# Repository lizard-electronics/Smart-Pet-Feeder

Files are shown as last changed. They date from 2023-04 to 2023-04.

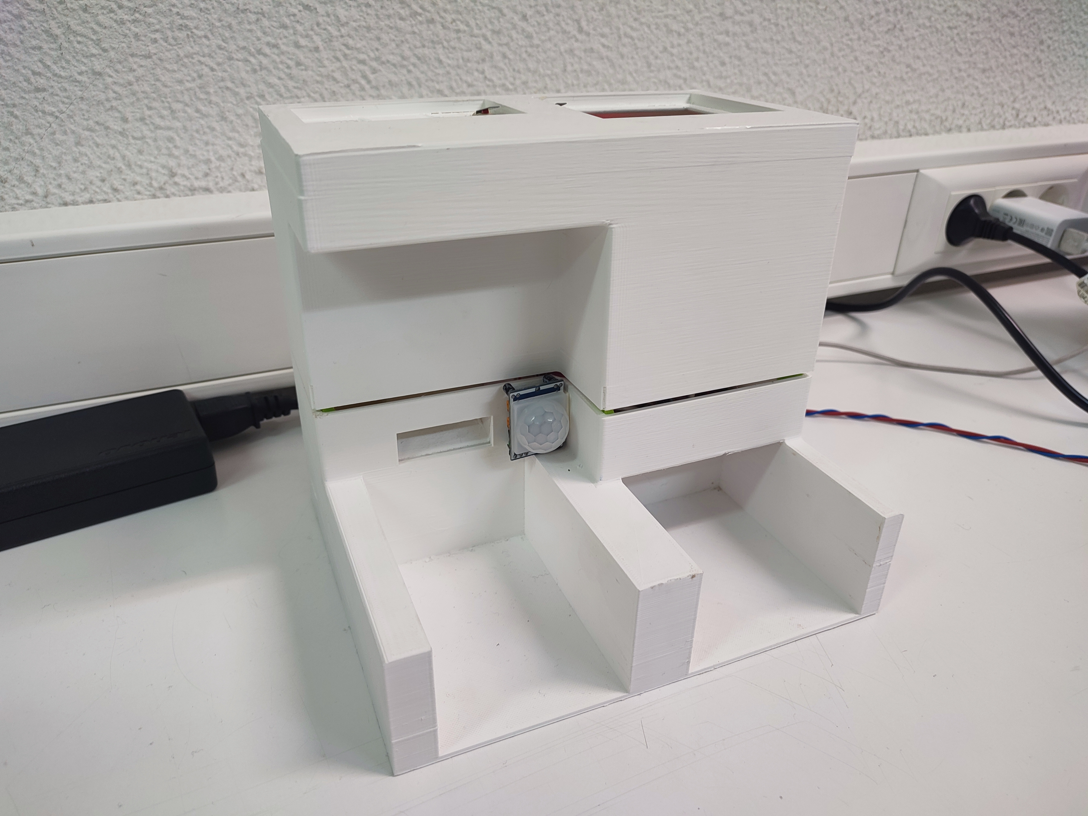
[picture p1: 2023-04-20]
Pictures/SmartPetFeeder_FinalResult.jpg

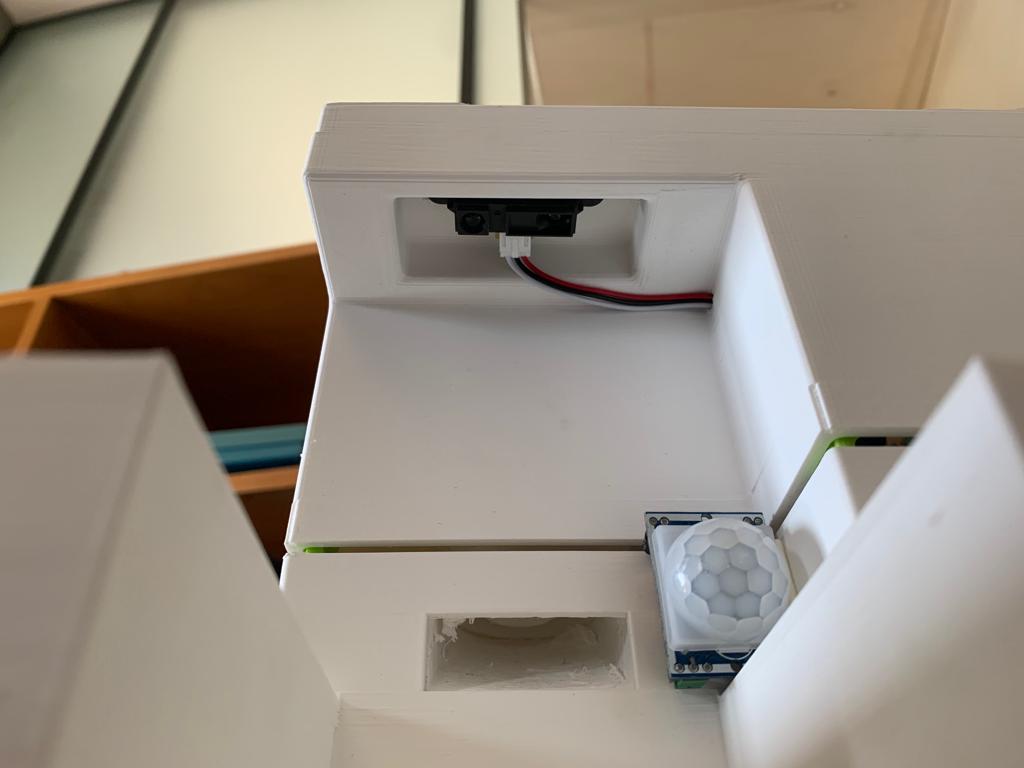
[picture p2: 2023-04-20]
Pictures/SmartPetFeeder_FoodSensor.jpg

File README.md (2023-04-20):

# Smart-Pet-Feeder

College project developed for the Internet of Things course.

Developed the firmware for an ESP32 using FreeRTOS to control the hardware and communicate through MQTT the Pet Feeder’s food and water status to a Data Base implemented on a Raspberry Pi (Node-RED).

*IPS - Escola Superior de Tecnologia de Setúbal*  
*Licenciatura em Engenharia Eletrotécnica e de Computadores*  
*Projeto de Internet das Coisas*  
2022/2023

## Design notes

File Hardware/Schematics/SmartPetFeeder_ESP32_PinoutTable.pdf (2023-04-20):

Name | Type | J2 | Left | Battery Up | Right | J1 | Name | Type
| | | NC | | NC
| POWER | 1 | 5V | | CLK
| | | CMD | | SD0
| | | SD3 | | SD1
| | | SD2 | | 15 | 1 | VALVE_WATER | GPIO_OUTPUT
SENSOR_PIR | GPIO_INPUT | 2 | 13 | 2 | RESERVED2 | GPIO
| POWER | | GND | | 0 | 2 | LED_NOTIFICATION | GPIO_OUTPUT
12 | 4 | 3 | LED_LEVEL | GPIO_OUTPUT
TRIG_DISPENSER | GPIO_OUTPUT | 4 | 14 | 16 | 4 | LED_STATE | GPIO_OUTPUT
ECHO_DISPENSER | GPIO_INPUT | 5 | 27 | | 17 | 5 | STEPPER_IN4 | GPIO_OUTPUT
| | 6 | 26 | | 5 | 6 | STEPPER_IN3 | GPIO_OUTPUT
| | 7 | 25 | | 18 | 7 | STEPPER_IN2 | GPIO_OUTPUT
SENSOR_WATER | GPIO_INPUT | 8 | 33 | | 19 | 8 | STEPPER_IN1 | GPIO_OUTPUT
SWITCH_LID | GPIO_INPUT | 9 | 32 | GND | POWER
SWITCH_BOWL | GPIO_INPUT | 10 | 35 | 21 | RESERVED21 | GPIO
BUTTON_MAINTENANCE | GPIO_INPUT | 11 | 34 | | RX
SENSOR_FOOD | GPIO_INPUT | 3 | SVN | | TX
SVP | 22 | RESERVED22 | GPIO
BUTTON_RESET | GPIO_INPUT | 12 | EN | 23 | RESERVED23 | GPIO
| POWER | 13 | 3V3 | | GND | 10,11,12 | | POWER

Buttons/Switches
Ultrassonic Level Sensors
PIR Sensor
Solenoid Valve
LEDs
Stepper Motor
5V
3V3
GND

ESP32

Color Legend

#define SENSOR_PIR_GPIO_INPUT 13 | #define VALVE_WATER_GPIO_OUTPUT 15

| #define RESERVED2_GPIO 2
#define TRIG_DISPENSER_ 12 | #define LED_NOTIFICATION_GPIO_OUTPUT 0

#define ECHO_DISPENSER_GPIO_OUTPUT 14 | #define LED_LEVEL_GPIO_OUTPUT 4

#define TRIG_FOOD_GPIO_INPUT 27 | #define LED_STATE_GPIO_OUTPUT 16

#define ECHO_FOOD_ 26 | #define STEPPER_IN4_GPIO_OUTPUT 17

#define TRIG_WATER_ 25 | #define STEPPER_IN3_GPIO_OUTPUT 5

#define ECHO_WATER_GPIO_INPUT 33 | #define STEPPER_IN2_GPIO_OUTPUT 18

#define SWITCH_LID_GPIO_INPUT 32 | #define STEPPER_IN1_GPIO_OUTPUT 19

#define SWITCH_BOWL_GPIO_INPUT 35

#define BUTTON_MAINTENANCE_GPIO_INPUT 34 | #define RESERVED21_GPIO 21

#define RESERVED22_GPIO 22 #define RESERVED23_GPIO 23

TRIG_FOOD
ECHO_FOOD
TRIG_WATER
ECHO_WATER

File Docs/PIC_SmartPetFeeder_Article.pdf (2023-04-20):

# Smart Pet Feeder

Escola Superior de Tecnologia de Setúbal Licenciatura em Engenharia Eletrotécnica e de Computadores, Projeto em Internet das Coisas

Eduardo Silva [Database] | 202001449@estudantes.ips.pt
Guilherme Correia [Mobile App] | 202002058@estudantes.ips.pt
João Reis [Node-RED & 3D Model] | 200500970@estudantes.ips.pt
Manuel Lagarto [Firmware] | 202002147@estudantes.ips.pt
Rui Colaço [Hardware] | 199100317@estudantes.ips.pt
I. INTRODUCTION

Most of the time, pet owners spend their time away from home and away from their pet friends, whether during vacation or work, leaving them a certain quantity of food and water which may get spoiled or be spilled away accidentally by the animal.

To solve these problems was created the Smart Pet Feeder, which provides pet owners with an innovative way to keep their furry friends well-fed, from monitoring their feeding habits to scheduling portion sizes based on veterinary advice.

This solution consists of the main device, the Pet Feeder that pairs with the Central Hub through a wireless connection. With this method, pairing more than one Pet Feeder to a single Central Hub is possible.

The Pet Feeder can feed both food and water, where the food is stored in an internal dispenser with an integrated stepper motor for precision portion control, and the water is regulated through a valve connected to the house’s water line. A set of sensors implemented in the Pet Feeder constantly monitors and transmits to the Central Hub the food and water levels in the bowls and dispenser, as well as the animal presence.

The Central Hub is implemented with a 7-inch display that displays each Pet Feeder’s dashboard. These dashboards show the levels of each Pet Feeder, as well as the important notifications and scheduled portions. All the data needed by the Central Hub and the rest of the systems are stored in the integrated database.

A mobile app for Android users is also available for the Smart Pet Feeder. With this app, pet owners can schedule portions based on veterinary advice, monitor feeding habits, control the connected devices, receive push notifications, and many more features that make the Smart Pet Feeder more interactive.

To summarize, the Smart Pet Feeder has different features that increase the quality of life of pets and allow pet owners more ease in feeding and monitoring the animal, for example:

- Scheduled portions of food and water.
- Pet Feeder’s state monitoring.
- Feeding habits monitoring.
- Mobile app notifications and warnings.
- Minimalist and compact design.
- Be integrated into the pet owner’s house or in an institution.

II. STATE OF THE ART

The industry of Smart Pet Feeders is increasing daily with many models appearing on the market with scheduling and monitoring capabilities, being one of the biggest takes of the Internet of Things revolution.

While most Smart Pet Feeders can only control the dispensed food based only a schedule defined by the pet owner, there are pet feeders that can also monitor the feeding habits, do self-tests, and integrate their data with the main Smart Home app. An example is the XIAOMI® Smart Pet Feeder.

On the other hand, one feature that all the Smart Pet Feeders available on the market share is providing pet owners the convenience and ease of feeding their furry friends, ensuring their pets are well-fed and hydrated even when their owners are away from home during vacation or work.

III. SYSTEM DESCRIPTION

The Smart Pet Feeder is based on two main components, the ESP32, and the Raspberry Pi microcontrollers, used in the Pet Feeder and Central Hub devices (Figure 1), respectively.

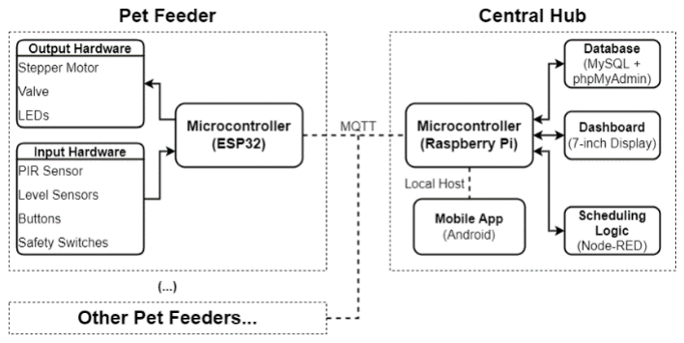
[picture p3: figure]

Figure 1 - Smart Pet Feeder Block Diagram.
The Pet Feeder is where the hardware to interface with the pet feeding process is implemented and has the following components: an ESP32, a Stepper Motor, a Valve, a PIR Sensor, two IR Level Sensors, an Ultrasonic Level Sensor, three LEDs, two Push Buttons and three Safety Switches.

The Central Hub is used to pair the installed Pet Feeders via the MQTT communication protocol and is where the scheduling control logic, Pet Feeder dashboard, and interface with the database are implemented. This device is composed of the Raspberry Pi and a 7-inch display.

Hardware
The Pet Feeder hardware schematic (Figure 2) was designed using KiCad, an open-source EDA software for hardware and PCB design.

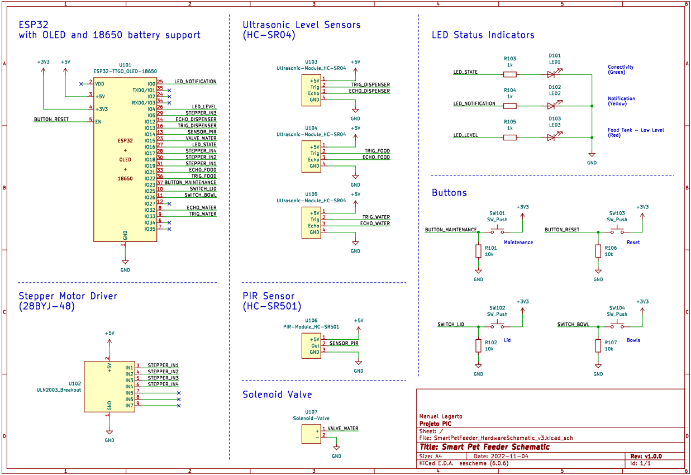
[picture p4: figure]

Figure 2 - Pet Feeder electrical hardware schematic.
The main control board integrates the ESP32 Board socket and all the screw-type terminal connectors for the sensors and actuators signals, allowing seamless maintenance and integration.

To rotate the paddle wheel to therefore control the amount of food purged through the nozzle, the 28BYJ-48 Stepper Motor, which pairs with the ULN2003 Driver, was selected. This Stepper Motor has four coil windings and delivers 64 steps per turn, corresponding to 5,625 degrees of precision. As the motor consumes about 217mA of current, the ESP32 board can’t supply the driver so an external power supply of 5V DC is required.

To regulate the water feeding was selected a generic one-way Solenoid Water Valve. An external power supply of 12V DC is required to command this valve.

As it is necessary three types of external power supply – main control board (5V), Stepper Motor (5V), and Solenoid Valve (12V) – a three-stage power supply was designed (Figure 3). The selected ESP32 board already has a 3.3V regulator.

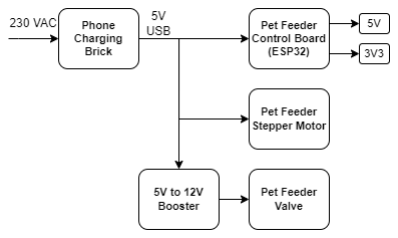
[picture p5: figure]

Figure 3 - Three-stage power supply.
For animal presence detection, the HC-SR501 PIR Sensor was selected, which uses an infrared LED. This sensor is placed at the front of the device and has 110 degrees of detection angle, supplied with 5V DC from the main control board.

Inside the Pet Feeder are placed three level
sensors. | Two | of them | are | the | SHARP
GP2Y0A21YK0F, mounted above the food and water bowls to measure its levels with infrared technology. These sensors offer better precision for harsh environments but are more expensive, so an HC-SR04 Ultrasonic Sensor was mounted inside the dispenser to measure its level, which is a closed and more controlled environment.

A set of LEDs and Buttons is mounted on the side of the Pet Feeder to give a user interface to the pet owner. A green LED indicates the state of the connectivity, a yellow LED indicates an unread notification, and a red LED indicates the low level of food in the dispenser. One of the buttons does a manual purge of the food and the other resets the system.

Three Safety Switches are mounted to stop the system in case one of the lids or the bowls are removed from the Pet Feeder.

Firmware
The firmware for the Pet Feeder is based on the dual-core ESP32 microcontroller and developed using the C++ programming language and the FreeRTOS operating system [www.freertos.org], natively supported by the Arduino framework.

All the firmware was developed with the Visual Studio Code code editor, with the extension PlatformIO to give it IDE capabilities to upload and debug the program in the ESP32.

The FreeRTOS is a real-time operating system used in embedded systems that require multi-tasking operation, and this project is no exception.

For this firmware, a set of tasks were created where the tasks related to the input/output hardware are pinned to the ESP32 Core0 (Figure 4 & Figure 5), and the tasks related to the MQTT communication are pinned to the ESP32 Core1 (Figure 6). With this method, it's possible to guarantee that the MQTT connectivity with the Central Hub is never interrupted.

Figure 4 - Input hardware FreeRTOS tasks.

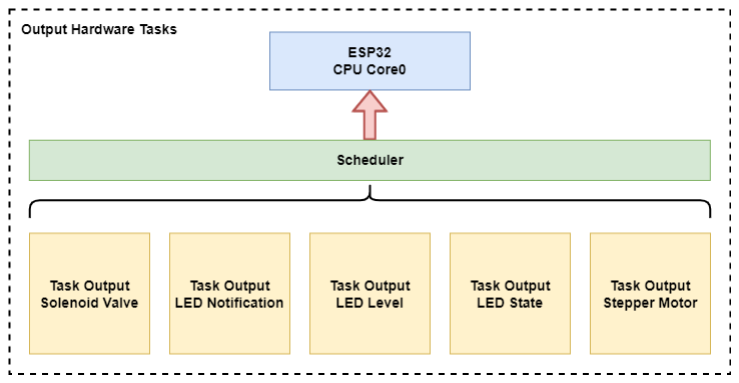
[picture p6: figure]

Figure 5 - Output hardware FreeRTOS tasks.

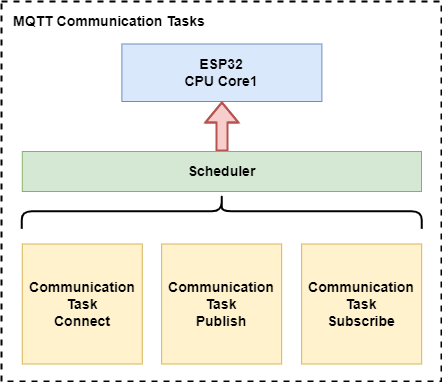
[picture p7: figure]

Figure 6 - MQTT communication FreeRTOS tasks.
To pass data between different tasks, a Queue Management API is available in FreeRTOS. With this method, it’s possible to safely pass information between the MQTT communication tasks and the I/O hardware tasks, by implementing the subscribe_queue and the publish_queue (Figure 7). The xQueueSend() function sends data to the queue, and the xQueueReceive() function waits for data to arrive in the queue.

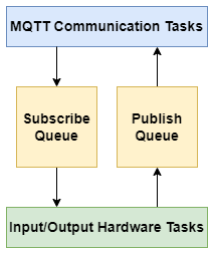
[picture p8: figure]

Figure 7 - Intertask communication diagram.
The MQTT protocol is largely used in IoT devices by using the server’s IP address, in this case, the Raspberry Pi installed on the Central Hub, to communicate over a wireless network connection. Each packet of communication data is composed of a topic and a message, i.e., the sensor id and the sensor data, respectively.

As seen in Figure 8, the Firmware flowchart is illustrated, representing the control algorithms and the interactions between each task. The complete code developed for the Firmware is attached at the end of this article.

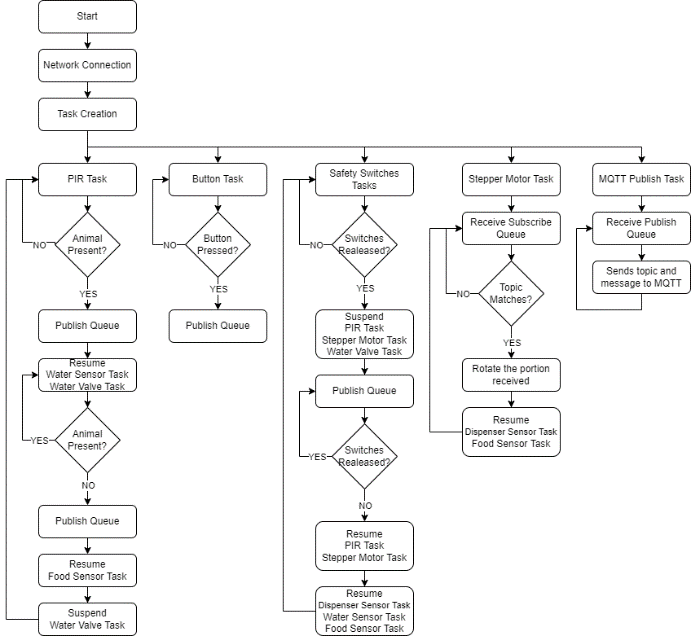
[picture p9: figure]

Figure 8 - Firmware's flowchart.
The interaction between each hardware task is done by the Task Control API available in FreeRTOS, which includes vTaskSuspend() and vTaskResume() functions. A task resumes its operation from the instant it was previously suspended.

Database
The Database for the Smart Pet Feeder stores all the data needed for the schedules of portions, pet owner login, feeding habits, pet information, and other important data for the system operation.

The relational model (Figure 9) was developed
with | the | ERDPlus | online | modeling | tool
(https://erdplus.com/). This model represents the tables (entities) used in the database to store the data, the data types of each attribute, and the relationships between each entity.

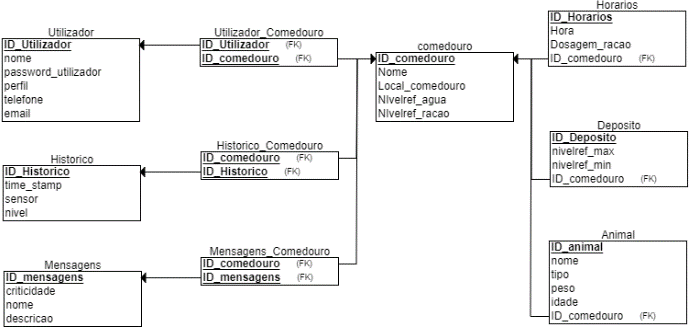
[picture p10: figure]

Figure 9 - Relation model planned for the Database.
Next, the Database was created with the MySQL Workbench software according to the previous model, using the DDL and DML languages.

To host and manage the created Database it was used the web application phpMyAdmin configured in the Raspberry Pi of the Central Hub, which makes use of .php scripts to a system interact with the Database. This application provides a web interface to manage and debug the Database which greatly eases the operation, creation, and maintenance of the Database.

Mobile App
With the Mobile App pet owners can have a personal user login to access the paired devices to the Central Hub, see the Pet Feeder status, schedule portions of meals based on the veterinary advice or animal’s metabolism, receive important notifications, and update the user information.

The app was developed with the Android Studio IDE using Java, JavaScript, HTML, and CSS programming languages. For the app was developed a flowchart (Figure 10) for the navigation between the different menus. After launching the app, the user will be prompted with the login screen that leads to the main page corresponding to the devices list. From this page, the user can access the side menu screen to access the other menus, such as schedule, feeder status, notifications, and devices list.

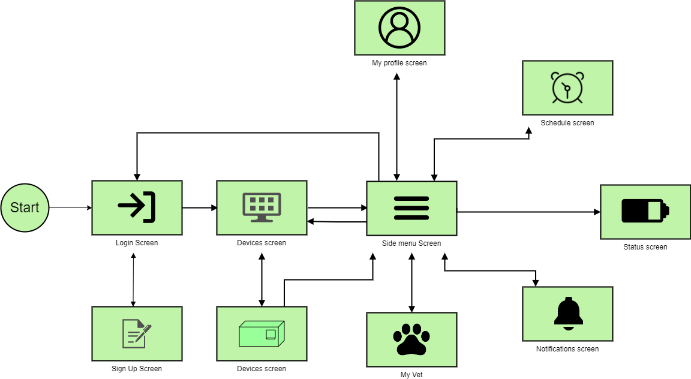
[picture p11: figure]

Figure 10 - Mobile App menu navigation flowchart.
To use this app, it’s necessary to always be connected to the same Smart Pet Feeder network because the app is constantly communicating with the database through the PHP functions, to realize queries and updates in the Database.

Figure 11 represents the user registration and login page menu in the app where the pet owner must insert his personal information.

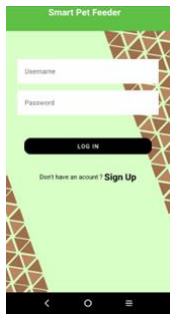
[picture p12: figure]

Figure 11 - Mobile App user registration and login page.
Figure 12 represents the Mobile App side panel where the user can navigate through all the menus available in the app.

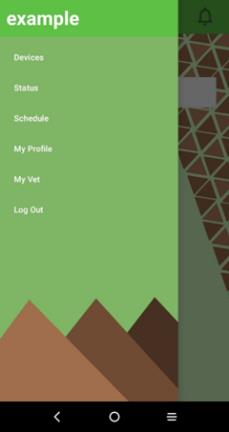
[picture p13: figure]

Figure 12 - Mobile App side panel.
Figure 13 represents the pairing process of a Pet Feeder to the Central Hub, by scanning its QR Code, and the menu of the paired device list.

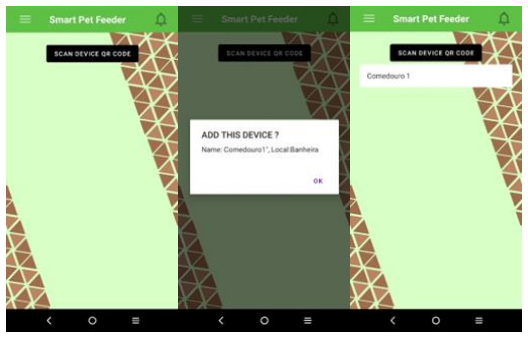
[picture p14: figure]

Figure 13 - Mobile App pairing process of a Pet Feeder.
Figure 14 represents the Pet Feeder’s status page where is shown the assigned name, bowls, and dispenser levels and its home location.

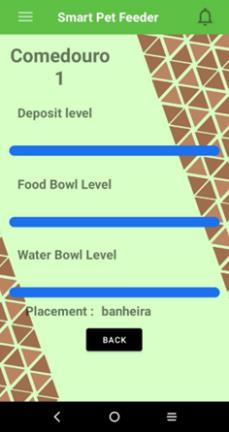
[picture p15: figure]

Figure 14 - Mobile App Pet Feeder's status page.
Figure 15 represents the animal’s scheduled meals where a new one can be added by inserting its time and portions.

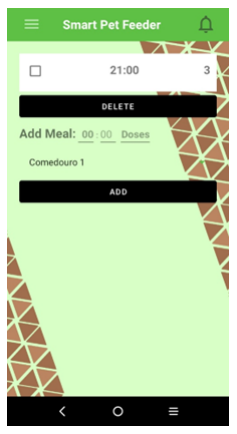
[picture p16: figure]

Figure 15 - Mobile App scheduled meals page.
Figure 16 represents the page to associate each animal to each Pet Feeder, by inserting their information and the pretended Pet Feeder id. On this page is also possible to view a list of the already associated animals to the app.

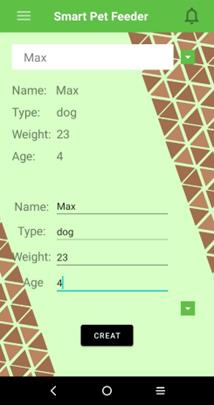
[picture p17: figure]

Figure 16 - Mobile App animal association page.
[Show the menu flow diagram. Explain each app menu]

Software (Node-RED)
Node-RED was used to program the control logic for the scheduling portions and other features of the Smart Pet Feeder. This tool is a web-based programming tool to connect different hardware devices to different APIs and online services.

For the control logic was developed a flowchart (Figure 17 & Figure 18) in which is represented the subscribe and publish functions from the MQTT, and the query/update process on the Database.

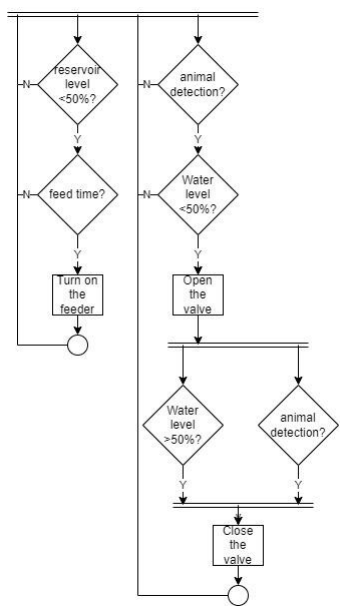
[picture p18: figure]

Figure 17 - Node-RED control logic flowchart, part I.

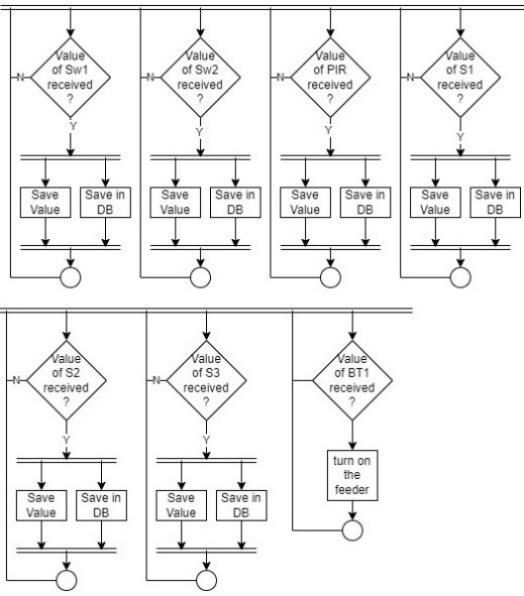
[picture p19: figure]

Figure 18 - Node-RED control logic flowchart, part II.
The control logic (called flows in the Node-RED) was programmed using various types of nodes available from the palette in the development environment of the programming tool. For this project, the two most important types of nodes were the “in/out mqtt” node and the “mysql” node, used to communicate with the Pet Feeder and the Database, respectively.

3D Model
The 3D Model of the Pet Feeder was designed with the Autodesk® Inventor CAD software and manufactured using a 3D printer with PLA filament.

In Figure 19 is represented the 3D front view of the Pet Feeder where the food bowl is located on the left and the water bowl is located on the right.

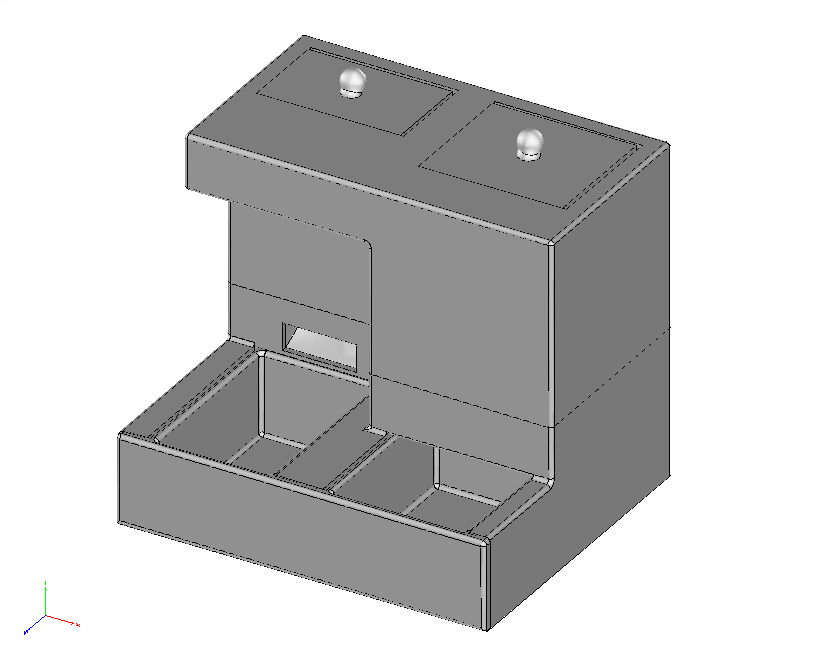
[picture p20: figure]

Figure 19 - Front view of the Pet Feeder’s 3D model.
In Figure 20 the same view is represented but with transparent faces to show the location of the dispenser and the feeding mechanism inside the Pet Feeder.

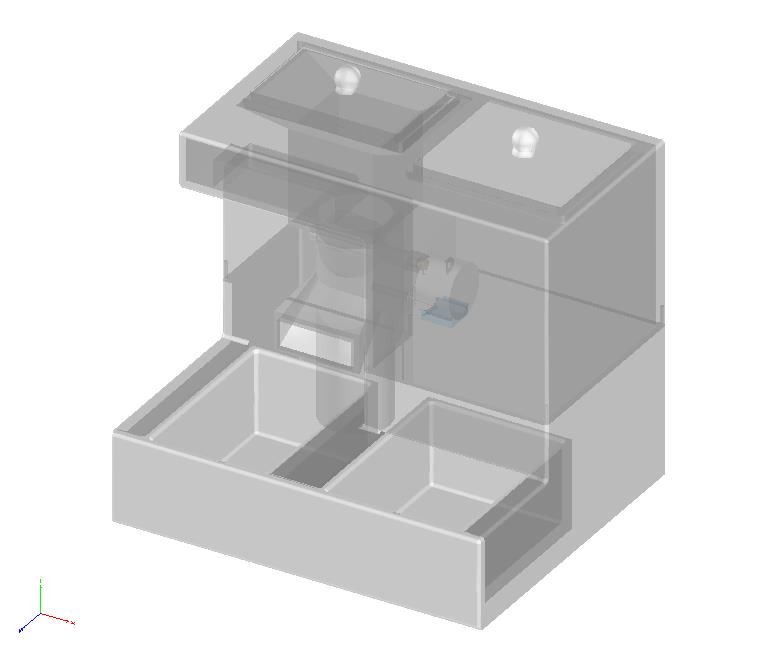
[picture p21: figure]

Figure 20 – Transparent view of the Pet Feeder’s 3D model.
In Figure 21 is represented a cut section of the side view of the Pet Feeder to represent the feeding mechanism under the dispenser.

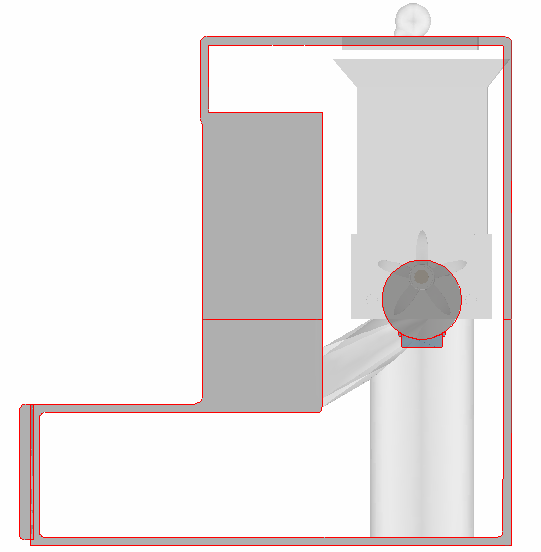
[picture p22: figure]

Figure 21 - Section cut of the Pet Feeder's 3D Model.
This mechanism is directly driven by the Stepper Motor and consists of a paddle wheel with five equally spaced blades that represent each portion of the animal’s food.

After collecting the food from the dispenser with the paddle wheel, the food is directed to a channel that leads to the front of the Pet Feeder, falling into the food bowl right under the exit.

Both the food and the water bowls are removable and integrated into the same part which eases the cleaning process.

IV. FINAL RESULTS

After 3D printing all the parts needed for the Smart Pet Feeder, the Pet Feeder’s model was assembled (Figure 22) with all the electrical hardware wired together and mounted inside (Figure 23).

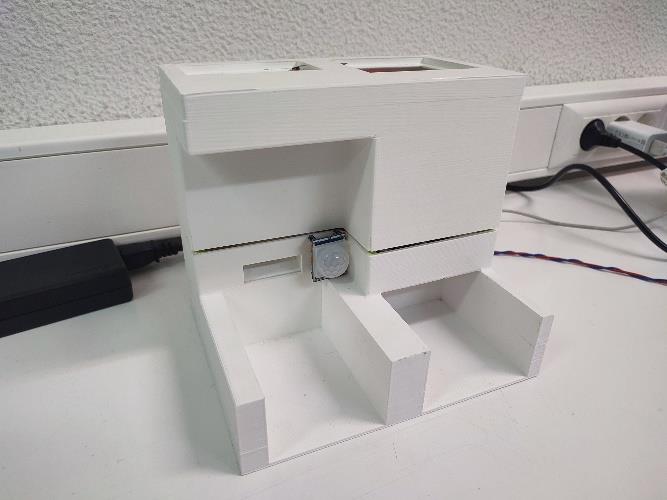
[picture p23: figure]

Figure 22 - Pet Feeder assembled.

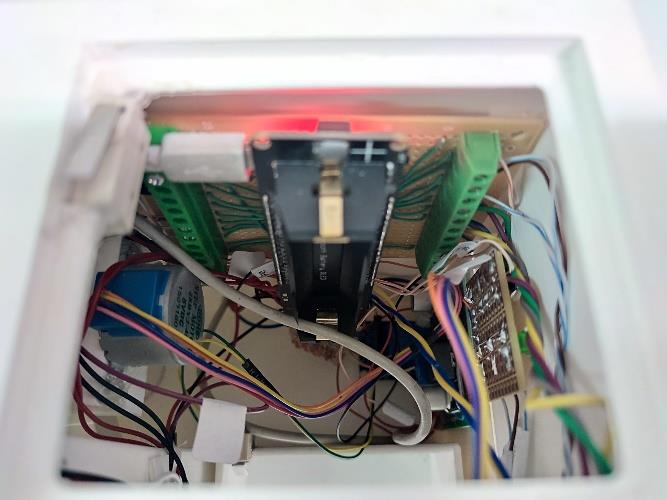
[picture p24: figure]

Figure 23 - Electrical hardware wired inside the Pet Feeder.
Figure 24 shows the LEDs and Buttons assembled on the side of the Pet Feeder, indicating the connected state (Green LED), low food level (Red LED), unread notifications (Yellow LED), manual feed (top button), and reset (bottom button).

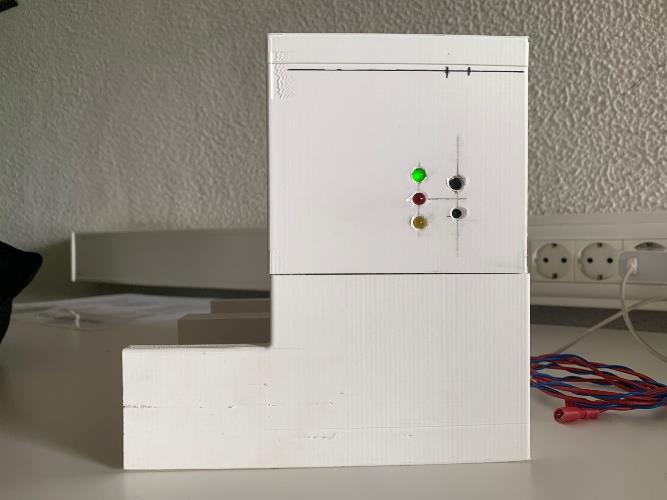
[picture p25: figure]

Figure 24 - LEDs and Buttons mounted on the side.

V. CONCLUSIONS & FUTURE UPDATES

With the development of this project, it was possible to acquire all the skills needed to develop an IoT product from the ground up.

This project addressed different topics that would not be possible to approach in this course. Hardware design where a schematic was designed with all the selected hardware for the project needs. Firmware development where the group was introduced to the FreeRTOS real-time operating system for the first time, which is used for an embedded system with multi-tasking operation. Database design by modeling an entire database according to the data needed for the project. Android app development where the group used Android Studio with different programming languages to develop the Mobile App for the pet owner to interact with the Smart Pet Feeder. Introduction of the Node-RED programming tool which was useful to integrate the different hardware devices with different APIs (Database for example). 3D Model development to 3D print the Pet Feeder concept model.

For the next iteration of the project, the Hardware needs to be integrated into a PCB board to achieve a more compact and eliminate noise in the wiring connections. The stepper motor also needs to be upgraded to a more powerful one, since it was detected a lack of force in the rotation of the paddle wheel during the tests.

VI. REFERENCES

1. KiCad EDA [Link] (https://www.kicad.org/)
2. Visual Studio Code [Link] (https://code.visualstudio.com/)
3. FreeRTOS documentation: [Link] (https://www.freertos.org/a00106.html)
4. ERDPlus database modeling tool [Link] (https://erdplus.com/)
5. Andriod Studio IDE [Link] (https://developer.android.com/studio)
6. Node-RED programming tool [Link] (https://nodered.org/)
7. 28BYJ-48 Stepper Motor datasheet [Link] (https://www.mouser.com/datasheet/2/758/stepd-01-data-sheet-1143075.pdf)
8. ULN2003 Driver datasheet [Link] (https://www.st.com/resource/en/datasheet/uln2001.pdf)
9. SHARP GP2Y0A21YK0F datasheet [Link] (https://global.sharp/products/device/lineup/data/pdf/datasheet/gp2y0a21yk_e.pdf)
10. HC-SR04 Ultrasonic Sensor datasheet [Link] (https://cdn.sparkfun.com/datasheets/Sensors/Proximity/HCSR04.pdf)
11. HC-SR501 PIR Sensor datasheet [Link] (https://www.epitran.it/ebayDrive/datasheet/44.pdf)

VII. ATTACHMENTS

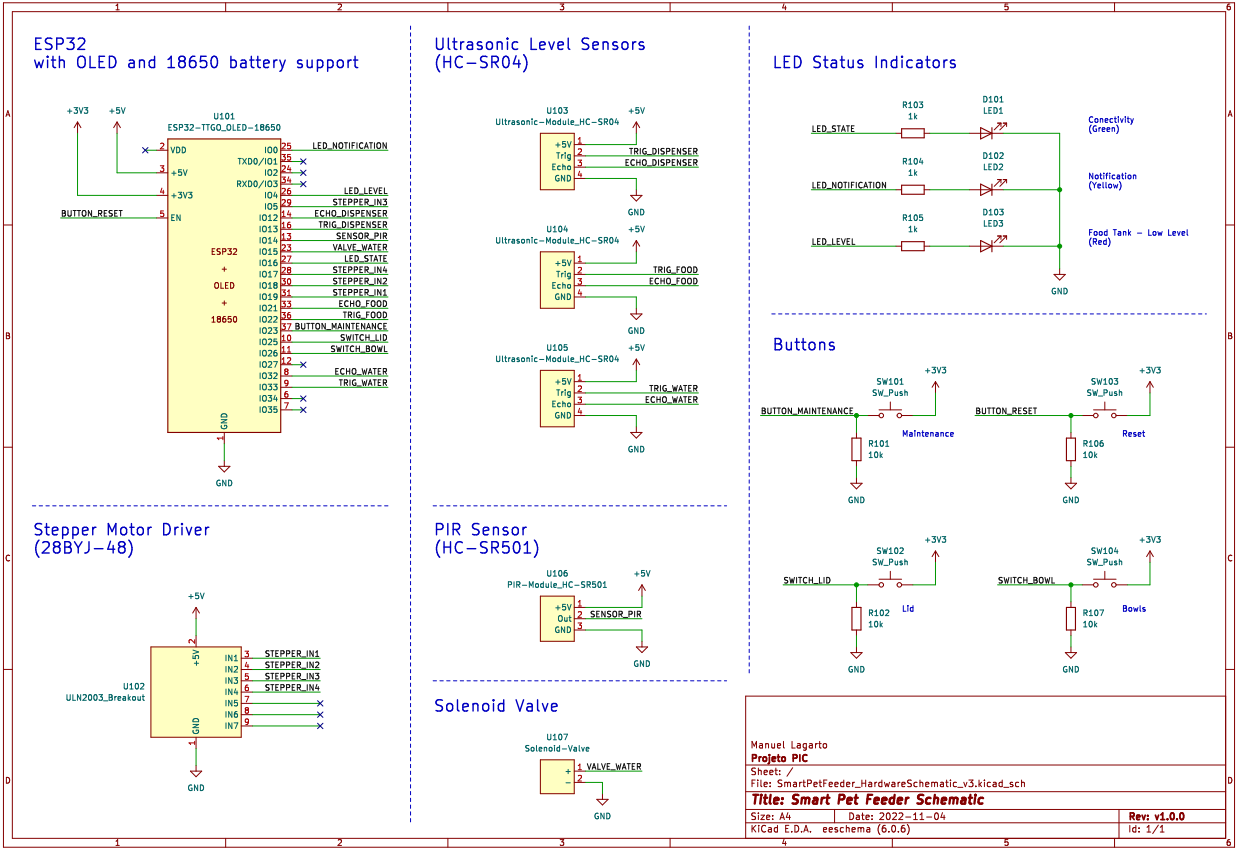
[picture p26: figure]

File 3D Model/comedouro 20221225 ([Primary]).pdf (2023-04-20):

setPageBoxes("Crop", 0, 0, [0,2000,2000,0]);

TITLE PART NO | comedouro 20221225 REVISION DESIGNER | LENOVO ENGINEER NOTES

THE INFORMATION AND/OR MATERIAL IN THIS DOCUMENT IS THE PROPERTY OF AND RESTRICTED INFORMATION AND/OR MATERIAL OF THE AUTHOR. THIS INFORMATION MAY NOT BE USED, REPRODUCED, PUBLISHED OR DISCLOSED TO OTHERS WITHOUT WRITTEN AUTHORIZATION. IT IS TO BE USED ONLY FOR MANUFACTURING ITEMS SPECIFIED WITHIN THE DOCUMENT.

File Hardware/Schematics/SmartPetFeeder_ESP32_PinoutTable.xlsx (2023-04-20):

Name | Type | J2 | Left | Battery Up | Right | J1 | Name | Type | #define SENSOR_PIR_GPIO_INPUT 13 | #define VALVE_WATER_GPIO_OUTPUT 15
 |  |  | NC | ESP32 | NC |  |  |  |  | #define RESERVED2_GPIO 2
 | POWER | 1 | 5V |  | CLK |  |  |  | #define TRIG_DISPENSER_ 12 | #define LED_NOTIFICATION_GPIO_OUTPUT 0
 |  |  | CMD |  | SD0 |  |  |  | #define ECHO_DISPENSER_GPIO_OUTPUT 14 | #define LED_LEVEL_GPIO_OUTPUT 4
 |  |  | SD3 |  | SD1 |  |  |  | #define TRIG_FOOD_GPIO_INPUT 27 | #define LED_STATE_GPIO_OUTPUT 16
 |  |  | SD2 |  | 15 | 1 | VALVE_WATER | GPIO_OUTPUT | #define ECHO_FOOD_ 26 | #define STEPPER_IN4_GPIO_OUTPUT 17
SENSOR_PIR | GPIO_INPUT | 2 | 13 |  | 2 |  | RESERVED2 | GPIO | #define TRIG_WATER_ 25 | #define STEPPER_IN3_GPIO_OUTPUT 5
 | POWER |  | GND |  | 0 | 2 | LED_NOTIFICATION | GPIO_OUTPUT | #define ECHO_WATER_GPIO_INPUT 33 | #define STEPPER_IN2_GPIO_OUTPUT 18
 |  |  | 12 |  | 4 | 3 | LED_LEVEL | GPIO_OUTPUT | #define SWITCH_LID_GPIO_INPUT 32 | #define STEPPER_IN1_GPIO_OUTPUT 19
TRIG_DISPENSER | GPIO_OUTPUT | 4 | 14 |  | 16 | 4 | LED_STATE | GPIO_OUTPUT | #define SWITCH_BOWL_GPIO_INPUT 35
ECHO_DISPENSER | GPIO_INPUT | 5 | 27 |  | 17 | 5 | STEPPER_IN4 | GPIO_OUTPUT | #define BUTTON_MAINTENANCE_GPIO_INPUT 34 | #define RESERVED21_GPIO 21
 |  | 6 | 26 |  | 5 | 6 | STEPPER_IN3 | GPIO_OUTPUT
 |  | 7 | 25 |  | 18 | 7 | STEPPER_IN2 | GPIO_OUTPUT
SENSOR_WATER | GPIO_INPUT | 8 | 33 |  | 19 | 8 | STEPPER_IN1 | GPIO_OUTPUT |  | #define RESERVED22_GPIO 22
SWITCH_LID | GPIO_INPUT | 9 | 32 |  | GND |  |  | POWER |  | #define RESERVED23_GPIO 23
SWITCH_BOWL | GPIO_INPUT | 10 | 35 |  | 21 |  | RESERVED21 | GPIO
BUTTON_MAINTENANCE | GPIO_INPUT | 11 | 34 |  | RX
SENSOR_FOOD | GPIO_INPUT | 3 | SVN |  | TX
 |  |  | SVP |  | 22 |  | RESERVED22 | GPIO
BUTTON_RESET | GPIO_INPUT | 12 | EN |  | 23 |  | RESERVED23 | GPIO
 | POWER | 13 | 3V3 |  | GND | 10,11,12 |  | POWER
Color Legend
Buttons/Switches
Ultrassonic Level Sensors |  |  |  |  |  |  |  |  | TRIG_FOOD
PIR Sensor |  |  |  |  |  |  |  |  | ECHO_FOOD
Solenoid Valve |  |  |  |  |  |  |  |  | TRIG_WATER
LEDs |  |  |  |  |  |  |  |  | ECHO_WATER
Stepper Motor
5V
3V3
GND

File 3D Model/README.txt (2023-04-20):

O ficheiro PDF do modelo 3D deve ser aberto com o programa Adobe Acrobat para ser possível interagir com o modelo.

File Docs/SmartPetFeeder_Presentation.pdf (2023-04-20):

# SMART PET


LEEC-PIC | 2022/2023 | Eduardo Silva, Guilherme Correia, João Reis, Manuel Lagarto, Rui Colaço

# FEEDER

Licenciatura em Engenharia Eletrotecnia e de Computadores

## Projeto de Internet das Coisas – 2022/2023

1

# O que é o Smart Pet Feeder?


2

# A Motivação

Existem neste momento,

# em Portugal, mais de 3,5 milhões de animais de companhia registados

### (SIAC - Sistema de Informação de Animais de Companhia)

### - Na atualidade as pessoas passam grande parte do seu tempo fora de casa, seja em trabalho ou em lazer

- Cada animal de estimação tem o seu próprio habito alimentar ou dieta
- Elevado número de abandono animal
- Instituições sobrelotadas e com recursos inadequados


3

# Como é que o Smart Pet Feeder vai fazer a diferença?

4


# Objectivo

### Dispensa e reposição automática de alimento

### Monitorização e gestão através de App Móvel e Desktop

### Gestão centralizada de mais que uma unidade terminal

5

# Mercado Alvo


Fonte: https://www.siac.vet/

# O Protótipo


6

7

# Arquitetura

do

# Smart Pet Feeder

# Visão Geral

8

9

# Diagrama de Blocos


10

# Arquitetura do Firmware (Inputs)


# Arquitetura do Firmware (Ouputs)


11


12

# Arquitetura do Firmware (MQTT)

13

# Arquitetura do Firmware (MQTT Queue)

14


# Diagrama

do

# Firmware

15

# Base de Dados - MR


16


# Node-RED

17

# Node-RED (Inputs MQTT)


18

# Node-RED (Outputs MQTT)

# Node-RED (Logic)


19


20

# Node-RED (Base de Dados)


21

# Node-RED (Dashboard)

22

# Node-RED (Dashboard Cockpit)

23

# Aplicação Móvel


- Receber notificações e avisos dos níveis das tigelas,

### reservatórios e comportamentos irregulares dos

animais;
- Visualizar dados com o histórico de refeições;
- Agendar as refeições do animal de estimação;

### - Definir o número de doses em cada refeição

# Aplicação Móvel


24


25

# Diagrama Eléctrico

# Construção do Protótipo

26

## Montagem da PCB - ESP 32

## Vista sensor de presença e nível da ração

## Montagem dos indicadores

## Fornecimento de água

## Vista geral

27


# VíDEO


28

# QUESTÕES


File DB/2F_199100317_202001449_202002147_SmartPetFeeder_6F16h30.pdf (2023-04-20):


## Smart Pet Feeder – Segunda Fase

## Projeto de Base de Dados – 2022/2023

Escola Superior de Tecnologia de Setúbal

Engenharia Eletrotécnica e de Computadores

Aluno 1: | 202001449 | Eduardo Silva
Aluno 2: | 202002147 | Manuel Lagarto
Aluno 3: | 199100317 | Rui Colaço
Docente: | Prof. Cláudio Miguel Sapateiro
Fase: | 02 | Data: | 2022/2023 | Turma: | LEEC-EC-02

Engenharia Eletrotécnica e de Computadores

## 1. Índice

## 2. Introdução

No âmbito da Unidade Curricular Projeto em Internet das Coisas, será

desenvolvido um projeto cuja componente de base de dados será incluída na

avaliação contínua da presente UC, Projeto de Base de Dados.

O projeto tem como objetivo o desenvolvimento de um comedouro inteligente para

animais, denominado por Smart Pet Feeder.

Este comedouro realizará a gestão automática das quantidades de ração e água

nas tigelas de alimentação com base nas parametrizações estabelecidas numa App

Móvel, dadas pelo utilizador responsável pelo animal.

Existirá adicionalmente um Hub Central composto por um Raspberry Pi, o qual,

será responsável pelo controlo de um ou mais comedouros a ele conectados, de

acordo com os dados na base de dados interna e com a lógica programada para o

processamento dos mesmos. Desta forma, o Hub Central será um dispositivo

indispensável para a correta operação do comedouro.

## 3. Especificação de Requisitos

### 3.1. Funcionalidades a Implementar no Projeto

3.1.1. Comedouro

Cada comedouro será composto pelos sensores e atuadores responsáveis pela

gestão das quantidades de ração e água nas tigelas. As quantidades serão

verificadas através de sensores de nível por ultrassons que, após o sensor de

presença ter detetado que o animal terminou a sua alimentação, estes reportam os

níveis para o Hub Central. Existirão três sensores de nível para cada tigela da ração

e água, e para o depósito interno da ração.

3.1.2. App Móvel

Através de uma App Móvel um ou mais utilizadores poderão gerir todos os

comedouros conectados ao Hub Central, permitindo assim, definir um nome para

cada comedouro, associar um animal ao mesmo, definir o local onde este se encontra

instalado, monitorizar os níveis das tigelas e do depósito interno, parametrizar tabelas

horárias para o enchimento da tigela de ração, visualizar um histórico da dieta do

animal e receber alertas/notificações sobre eventos diversos, tais como, depósito

interno quase vazio, falta de alimentação do animal, entre outros.

Cada perfil de utilizador criado na app será definido pelos dados de registo, assim

como, níveis de acesso diferentes para a utilização de certas funcionalidades da app.

Será possível também criar um perfil para cada animal que será associado a um

comedouro. Cada perfil será composto pelo nome do animal, peso, tipo (cão ou gato),

idade e a dosagem de ração para os períodos de alimentação.

3.1.3. Hub Central

O Hub Central será responsável por estabelecer uma conexão entre cada

comedouro e a App Móvel, assim como, por guardar, com recurso a uma base de

dados interna, todos os dados descritos nos tópicos anteriores.

No Hub Central também será implementada a lógica de controlo responsável por

fazer a leitura dos dados recebidos de cada comedouro, pelo processamento lógico

dos dados, e por enviar os dados para os atuadores de cada comedouro.

### 3.2. Identificação das Entidades e Atributos

Foi dado início ao desenvolvimento do Modelo Entidade-Relação da base de

dados do projeto com a identificação das seguintes entidades:

1. Utilizador – dados de login do utilizador;
2. Comedouro – dados de identificação do comedouro, animal atribuído e

níveis de referência paras as tigelas da água e da ração;

3. Animal | – dados do perfil de cada animal associado a um comedouro.
4. Depósito | – níveis de referência máximo e mínimo do depósito interno de

ração do comedouro;

5. Horários | – periodicidade e hora de cada refeição;
6. Histórico | – dados com o time stamp da leitura do nível de cada sensor de

cada comedouro;

7. Mensagens – mensagens modelo com nome, descrição e níveis de

criticidade para cada notificação na app;

Para a entidade Utilizador foram definidos os seguintes atributos:

1. id | – chave primária;
2. nome | – nome do utilizador;
3. password | – password de login do utilizador;
4. perfil | – nível de controlo de acesso na app;
5. telefone | – número de telemóvel/telefone do utilizador;
6. email | – endereço de e-mail do utilizador;

Para a entidade Comedouro foram definidos os seguintes atributos:

1. id | – chave primária;
2. nome | – nome atribuído ao comedouro;
3. local | – local da habitação onde se encontra o comedouro;
4. nivelref_água – nível máximo de referência para a tigela da água;
5. nivelref_racao – nível máximo de referência para a tigela da ração;
6. Utilizador – um ou mais utilizadores aos quais a um ou mais comedouros

estão atribuídos.

Para a entidade Animal foram definidos os seguintes atributos:
1. id | – chave primária;
2. nome | – nome do animal;
3. tipo | – cão ou gato;
4. peso | – peso do animal;
5. idade | – idade do animal;
6. dosagem_racao – dose de ração para cada período de alimentação.
7. Comedouro – um único comedouro ao qual um único animal está atribuído.

Para a entidade Depósito foram definidos os seguintes atributos:
1. id | – chave primária;
2. nivelref_max– nível máximo de referência do depósito interno do comedouro;
3. nivelref_min – nível mínimo de referência do depósito interno do comedouro;
4. Comedouro – um único comedouro ao qual um único depósito está atribuído.

Para a entidade Horários foram definidos os seguintes atributos:
1. id | – chave primária;
2. periodicidade – frequência a que se repete o horário;
3. hora | – hora definida para a alimentação do animal;
4. Comedouro – um ou mais comedouros aos quais um ou mais horários estão

atribuídos.

Para a entidade Histórico foram definidos os seguintes atributos:
1. id | – chave primária;
2. time_stamp – registo da data e hora da recolha de dados do sensor;
3. sensor | – id do sensor ao qual corresponde o nível recolhido;
4. nível | – valor do nível recolhido;
5. Comedouro – um ou mais comedouros aos quais poderá ou não um histórico

estar atribuído.

Para a entidade Mensagens foram definidos os seguintes atributos:
1. id | – chave primária;
2. criticidade | – nível de criticidade da mensagem (alerta ou notificação);
3. nome | – título da mensagem;
4. descrição | – descrição da mensagem;
5. Comedouro – zero ou mais comedouros aos quais uma ou mais mensagens estão atribuídas.

### 3.3. Relaçõesentre Entidades (MER)

Através das entidades e atributos apresentados no tópico anterior, foi possível

estabelecer os relacionamentos entre entidades e as respetivas restrições.

Para o relacionamento entre Utilizador e Comedouro, um Utilizador pode ter zero

ou vários Comedouros (0N) e um Comedouro pode ter um ou vários Utilizadores (1N).

Para o relacionamento entre Comedouro e Animal, um Comedouro apenas pode

ter um único Animal (1) e um Animal apenas pode ter um único Comedouro (1).

Para o relacionamento entre Comedouro e Depósito, um Comedouro apenas

pode ter um único Depósito (1) e um Depósito apenas um único Comedouro (1).

Para o relacionamento entre Comedouro e Horários, um Comedouro pode ter um

ou vários Horários (1N) e um Horário pode ter um ou vários Comedouros (1N).

Para o relacionamento entre Comedouro e Histórico, um Comedouro pode ter um

ou vários Históricos (1N) e um Histórico pode ter zero ou vários Comedouros (0N).

Para o relacionamento entre Comedouro e Mensagens, um Comedouro pode ter

uma ou vários Mensagens (1N) e uma Mensagem pode zero ou vários Comedouros

(0N).

## 4. Diagrama Entidade-Relação (DER)

### 4.1. Proposta Inicial

Na Figura 1 em anexo encontra-se representado o Diagrama ER desenvolvido

com recurso ao software draw.io.

No diagrama encontram-se representadas as entidades com os respetivos

atributos analisados nos tópicos anteriores, assim como, a simbologia para a

identificação das relações e restrições entre entidades.

### 4.2. Revisões ao DER

Após a realização da discussão da fase anterior do projeto, foi necessário realizar

alterações ao Diagrama Entidade-Relação. As alterações corresponderam à

eliminação do atributo dosagem_racao na entidade Animal, e à alteração do atributo

periodicidade para dosagem_racao na entidade Horários.

Esta alteração deveu-se ao facto do atributo periodicidade ser redundante num

horário visto este ser baseado numa hora definida pelo utilizador. Em relação ao

atributo dosagem_racao, concluiu-se queseria mais lógico a quantidade de dosagens

estar associada a um horário ao invés de um animal.

O novo Diagrama Entidade-Relação encontra-se representado na Figura 2 em

anexo.

## 5. Modelo Relacional (MR)

Em seguida, com recurso ao software ERDPlus, foi desenvolvido o Modelo

Relacional de acordo com as relações estabelecidas entre entidades e o Diagrama

Entidade-Relação apresentado no tópico anterior.

Este modelo encontra-se representado na Figura 3 em anexo e permite

representar como serão compostas cada tabela, correspondentes a cada entidade da

base de dados do projeto, com os respetivos atributos, chaves primárias e chaves

estrangeiras representadas.

Neste modelo também foram representadas as tabelas resultantes das relações

de muitos para muitos, correspondentes às tabelas Utilizador_Comedouro,

Historico_Comedouro e Mensagens_Comedouro, onde foram incluídas como chaves

estrangeiras as chaves primárias de cada entidade da relação. Nas restantes

entidades Horarios, Deposito e Animal, foi incluída como chave estrangeira a chave

primária da entidade Comedouro.

## 6. Scripts Desenvolvidos

Em anexo ao ficheiro do relatório seguem quatro ficheiros texto desenvolvidos,

com recurso ao software MySQL, para a criação de tabelas (create.txt), para a

inserção de dados nas tabelas (populate.txt), para a inserção de dados errados para

que falhem a introdução nas tabelas (populateErros.txt) e para as consultas dos

dados inseridos (consultas.txt).

### 6.1. Criação das Tabelas

Para a criação das tabelas foi utilizada a linguagem de definição de dados DDL,

através da instrução “CREATE TABLE”. A definição das chaves primárias em cada

tabela foi dada através da instrução “PRIMARY KEY (atributo)”, sendo que cada

chave primária apresenta como restrições “NOT NULL” e “AUTO_INCREMENT”. A

definição das chaves estrangeiras foi dada através da instrução “FOREIGN KEY

(atributo) REFERENCES (…)”. Nas tabelas de entidades referenciadas, foi

implementada a restrição “ON DELETE CASCADE” e “ON UPDATE CASCADE”. De

notar que, o processo de criação das tabelas teve como base o modelo relacional

apresentado no tópico 5.

### 6.2. Inserção de Dados

Em cada tabela foram inseridos diversos dados de teste com a utilização da

linguagem de manipulação de dados DML, através da instrução “INSERT INTO”.

Como o projeto Smart Pet Feeder não foi finalizado até à data de entrega do

presente projeto, a base de dados ainda não estava integrada com o restante sistema,

logo, os dados inseridos correspondem a uma aproximação da realidade com o

objetivo de serem simuladas as consultas da base de dados.

### 6.3. Inserção de Erros

Foram também introduzidas falhas na inserção, remoção e atualização dos

dados, por forma a testar as falhas relacionadas com o desrespeito às restrições

definidas no modelo relacional e na criação das tabelas.

Ao todo foram introduzidas cinco falhas, sendo que, o código de cada uma

encontra-se devidamente comentado no script “populateErros.txt”, em anexo ao

presente relatório.

### 6.4. Consulta das Tabelas

Para as consultas da base de dados foi utilizada a linguagem DML em que, com

base nos requisitos impostos pelo guia do projeto, foram desenvolvidas doze

consultas.

As consultas foram desenvolvidas com o objetivo de simular as consultas

realizadas pela aplicação móvel e pela lógica de controlo implementada no ambiente

de desenvolvimento Node-RED, em operação no Hub Central.

## 7. Conclusão

Com a conclusão do Projeto de Base de Dados referente ao projeto Smart Pet

Feeder inserido na UC de Projeto em Internet das Coisas, foi possível desenvolver

uma base de dados pronta a ser integrada no sistema de um comedouro inteligente

para animais.

Este projeto foi composto por várias etapas de desenvolvimento, das quais, a

especificação de requisitos e o desenvolvimento do Diagrama Entidade-Relação que

foram inseridas na primeira fase, e na segunda fase o desenvolvimento do Modelo

Relacional e dos scripts com recurso ao software MySQL. Entre a primeira fase e a

segunda existiu um momento de autoavaliação do projeto que permitiu a identificação

de possíveis ajustes ao mesmo.

Posteriormente ao desenvolvimento da primeira iteração do Modelo e do

Diagrama Entidade-Relação da base de dados, foram identificadas lacunas

relacionadas com a falta de atributos importantes em certas entidades, dos quais, na

entidade Depósito a ausência de atributos para níveis de referência nos depósitos

internos de cada comedouro, e a substituição do atributo periodicidade para

dosagem_racao na entidade Horários. Após a correção destas lacunas procedeu-se

à continuação do desenvolvimento das restantes etapas.

Como não foi possível finalizar o projeto Smart Pet Feeder até à data de entrega

do presente Projeto de Base de Dados, não foi possível integrar a mesma com o

restante sistema do comedouro inteligente. Em falta, ficaram a realização de testes

em contexto prático, os quais, foram realizados durante as semanas seguintes à data

de entrega.

## 8. Anexos


Figura 1 - Primeira iteração do Diagrama Entidade-Relação.

Figura 2 - Segunda iteração do Diagrama Entidade-Relação.


Figura 3 - Modelo Relacional da base de dados do projeto.

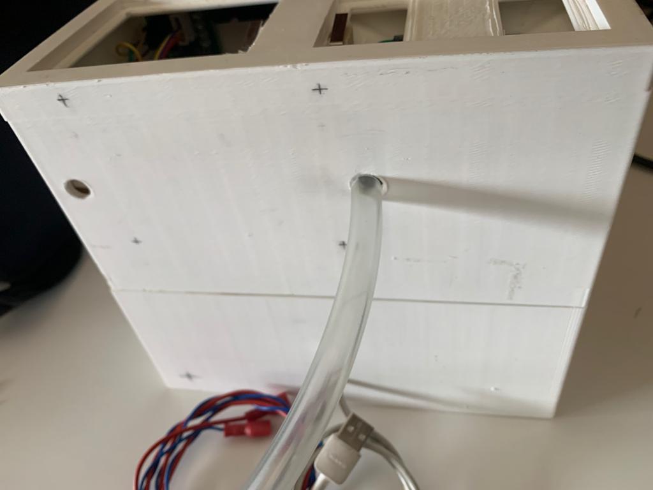
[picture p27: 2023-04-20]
Pictures/SmartPetFeeder_BackWaterFitting.jpg

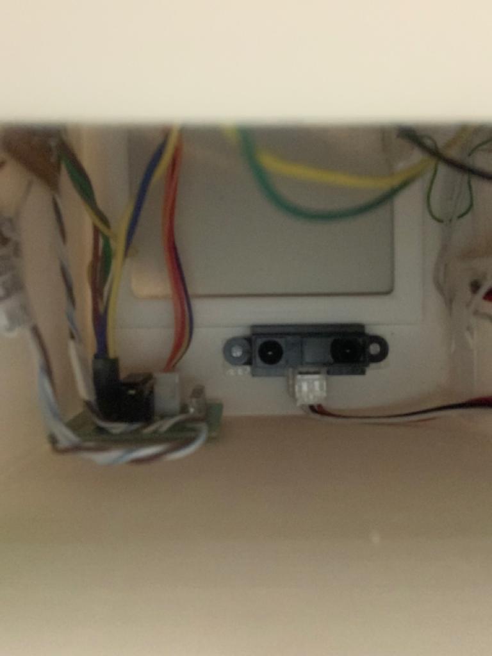
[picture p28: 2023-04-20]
Pictures/SmartPetFeeder_WaterSensor.jpg

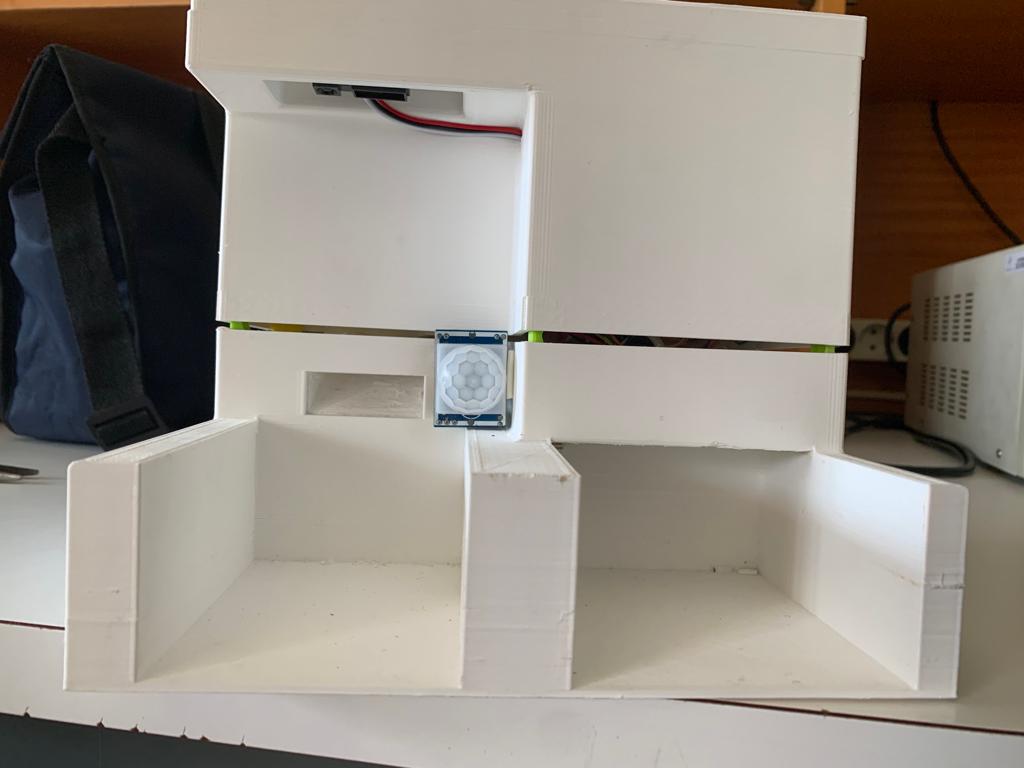
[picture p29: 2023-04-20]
Pictures/SmartPetFeeder_FrontView.jpg

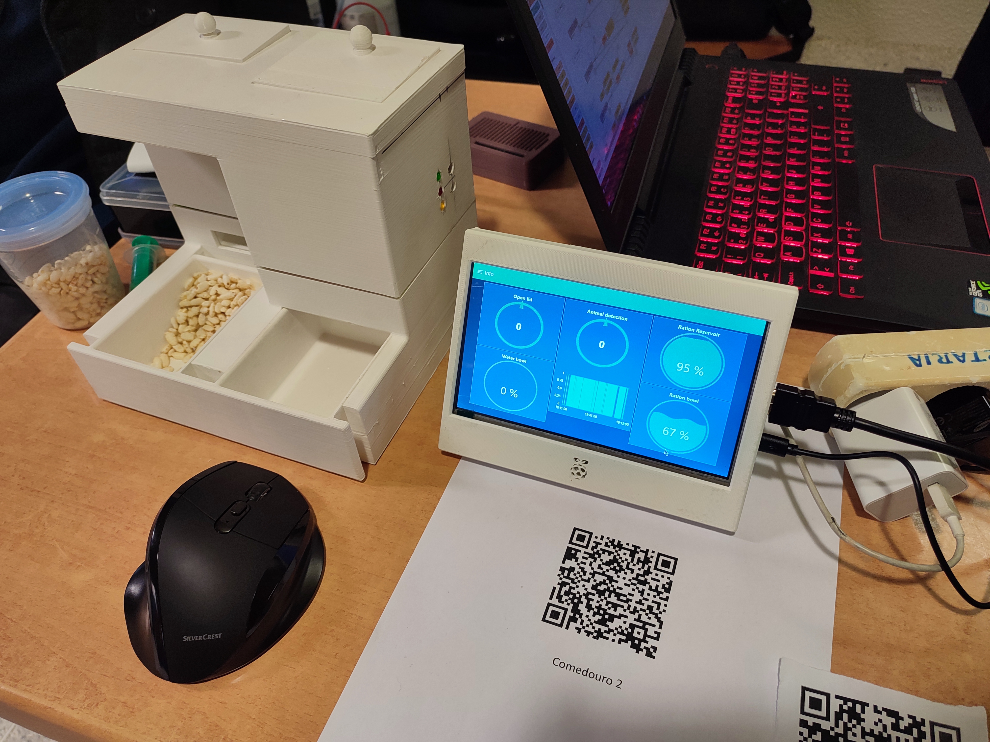
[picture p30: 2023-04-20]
Pictures/SmartPetFeeder_PresentationDay.jpg

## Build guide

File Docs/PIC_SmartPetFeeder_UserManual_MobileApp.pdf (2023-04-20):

# SMART PET FEEDER

ANDROID APP

USER MANUAL

P 1 | 20

# Index

P 2 | 20

# 1. Log in Screen

When the installation of the app is completed, and the user start the app for the first time, the Log in screen will appear, Fig.1.

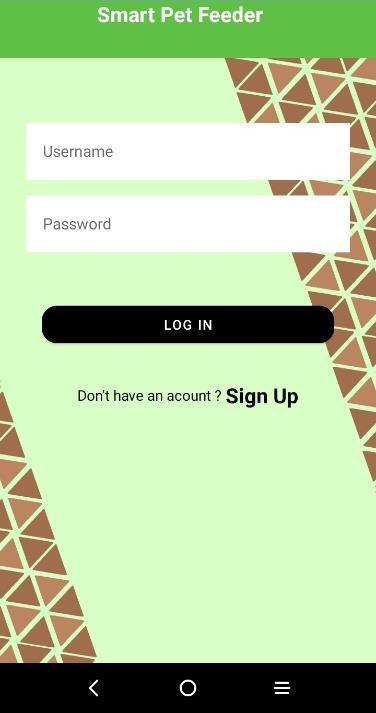
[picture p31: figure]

Figure 1 Log in Screen

If the user already has an account, he can fill the form with his username and his password and press the button LOG IN. In case the user still doesn’t have an account yet, he can press on Sign Up to redirect to the Registration Screen, Fig.4, where he can create his own account.

To log in in the app the user must fill all the input spaces and guarantee that the information match with his profile, Fig.2, only then if the log in is made successfully it will appear a small text on the bottom of the screen, Fig.3, then the Devices Screen will appear on the device, Fig.8.

If the information inserted is correct ant nothing happen then try to reset the app and check if the WI-FI connection is turned On and check if it is the same as the HUB.

Figure 2 Log in validation | Figure 3 Log in Successful

P 3 | 20

# 2. Registration Screen

By pressing Sign Up on the Log in Screen, Fig.1, the Registration Screen will appear, Fig.4.

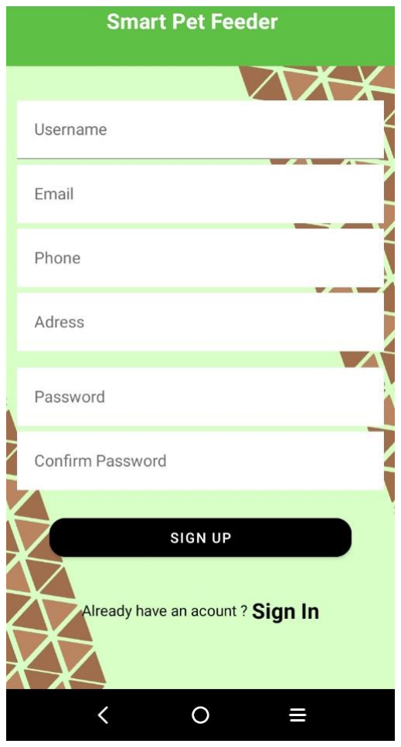
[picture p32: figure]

Figure 4 Registration Screen

In the Registration Screen the user can create an account by filling the form. In case one of them isn’t filled or correctly filled and the user press the SIGN UP button, it will appear the space in cause with a red colour, Fig.5. If the passwords spaces don’t match then a message in the bottom of the screen, Fig.6, will appear which means that the form with username, email, phone number and address are valid and only the passwords need to be verified.

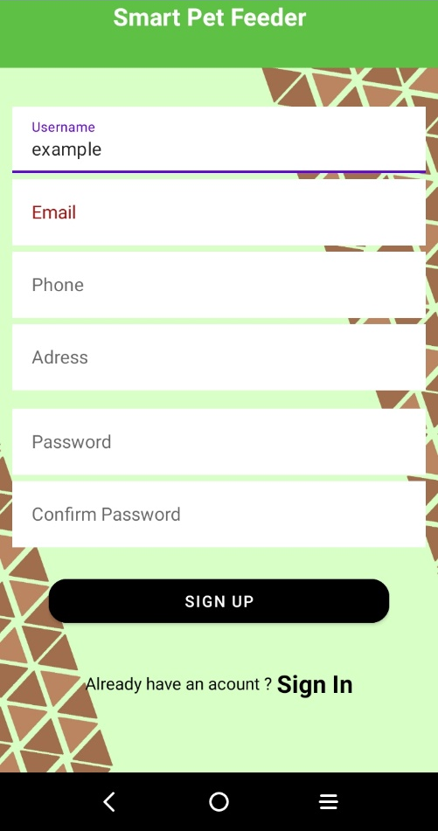
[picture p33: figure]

P 4 | 20

Figure 6 Registration form validation

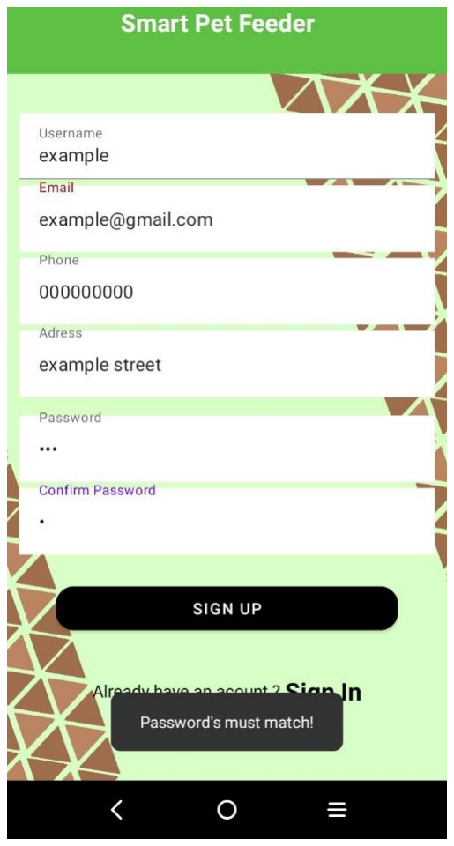
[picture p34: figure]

If the form and passwords are correctly filled and the user press the SIGN UP button than a message on the bottom of the screen, Fig.7, will appear and the Log in Screen.

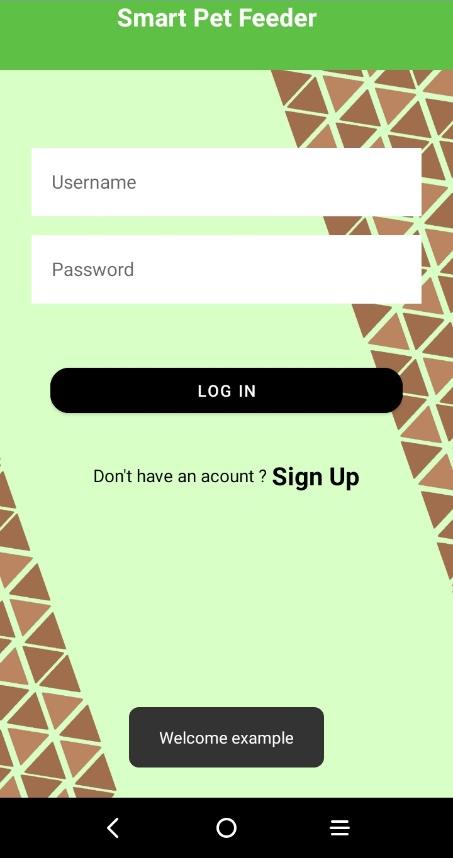
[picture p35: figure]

Figure 7 Registration successful

Figure 5 Registration password validation

P 5 | 20

# 3.Devices Screen

After the user logged in, the Devices Screen will appear, Fig.8. On this screen the user can see all the feeder devices paired with his account.

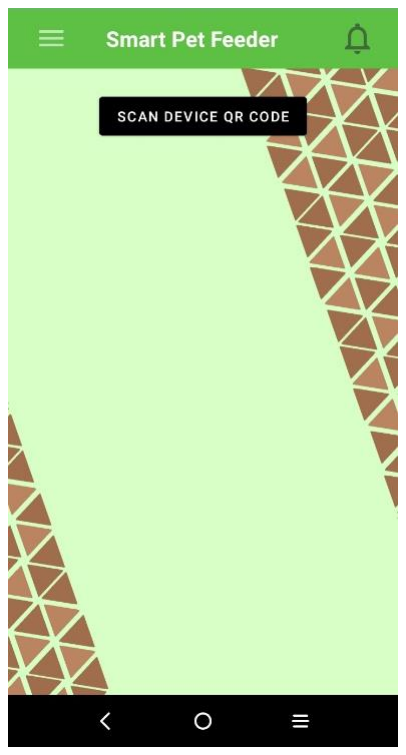
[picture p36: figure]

Figure 8 Devices screen

### 3.1 Pair to a feeder device

To pair a feeder device to the account, the user must press the SCAN DEVICE QR CODE button and allow the app to have access to the camera. To finish the pairing process the user must scan the QR code exposed on the feeder device, then a popup on the app will appear asking showing the feeder device info, Fig.9, after that press OK and the new feeder device will appear on the Devices Screen, Fig.10.

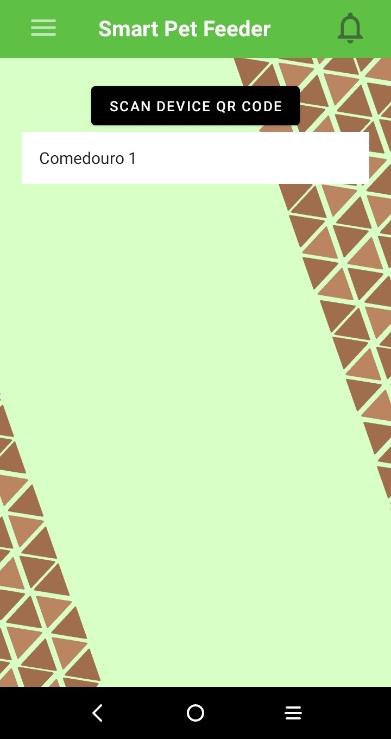
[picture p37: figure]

Figure 9 Confirm pair feeder device | Figure 10 Device Screen after adding device

P 6 | 20

### 3.2 Check current data from a feeder device

Once the user pairs at least one feeder device to their account, the user can press it to change the Devices Screen to show the name of the feeder device, the current level of the food deposit, food bowl and water bowl, Fig.11.

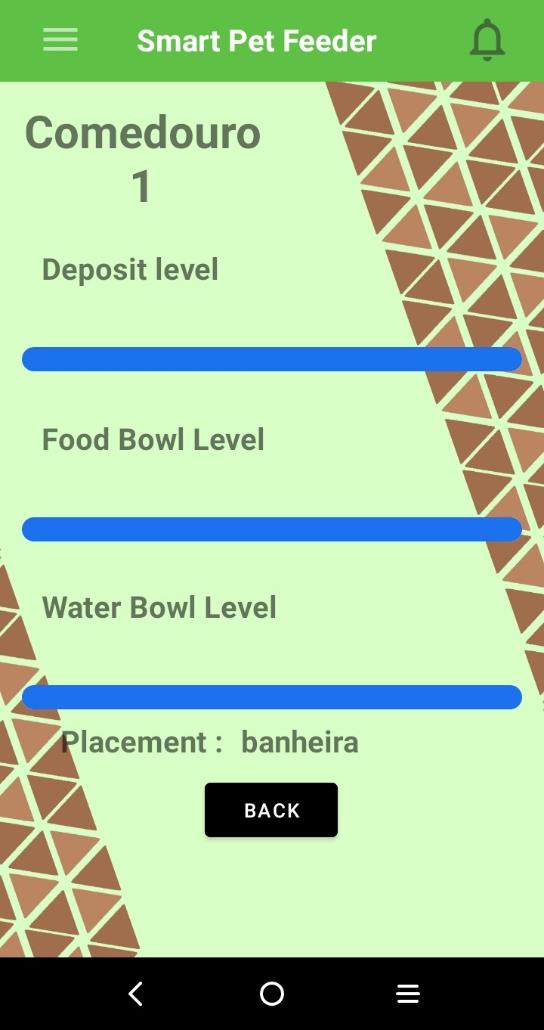
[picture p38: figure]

Figure 11 Feeder device selected

P 7 | 20

# 4. Side bar menu

The Side bar menu is a navigation menu, Fig.12, where the user can select the screen that he pretends to use and log out his session. The Side bar menu can be accessed from every screen if the user is logged, which means, every screen except the Log in Screen and the Registration Screen.

On the Side bar menu, it’s also possible to see the username of the user on the top left of the screen.

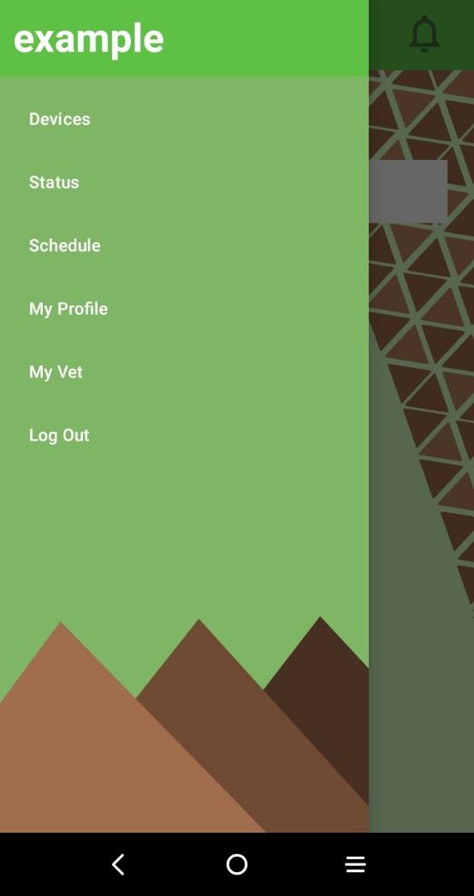
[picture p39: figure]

Figure 12 Side bar menu

### 4.1 Log out actions

Pressing on Log Out option, the account logged in will be disconnected on the app and the user will be transferred to the Log In Screen.

Closing the app on the user’s phone will cause the same effect of the Log Out option.

P 8 | 20

# 5. Status Screen

On the Status Screen, Fig.13, which can be accessed by Side bar menu, it’s possible to select which feeder device the user wants to check their status.

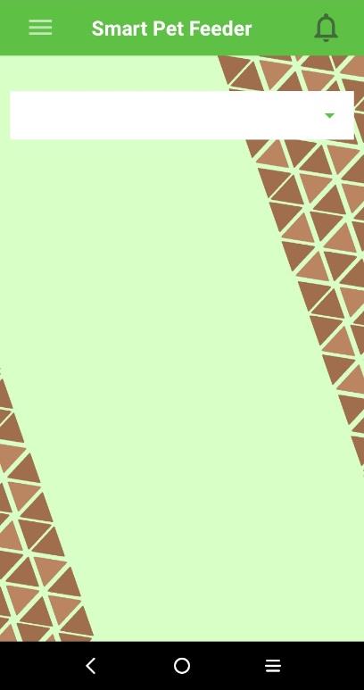
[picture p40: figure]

Figure 13 Status Screen

The selection is made by the select box on the Status Screen. Once the user select the device a message with the feeder device name, will appear on the bottom of the screen. The screen will automatically change, showing the number of times the animal ate, drank and the number of times the food bowl has refill, Fig.14.

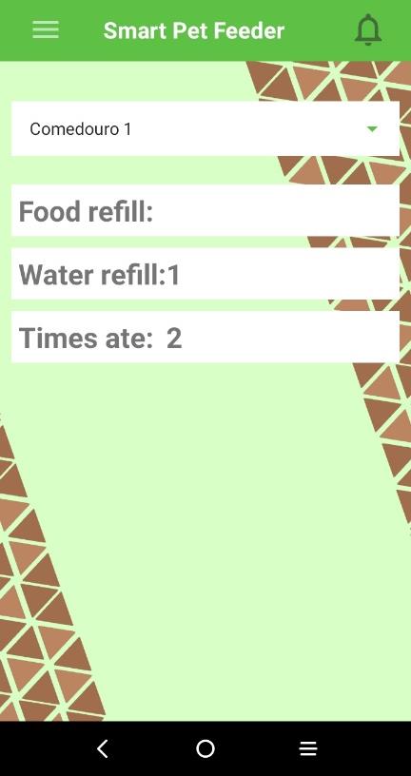
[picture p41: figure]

Figure 14 Status selected feeder device

P 9 | 20

# 6. Schedule Screen

In the Schedule Screen, Fig.15, the user can see all the meals that are currently schedule for their pet, showing the exact time (hh:mm) of the meal with the number of meals int that same meal.

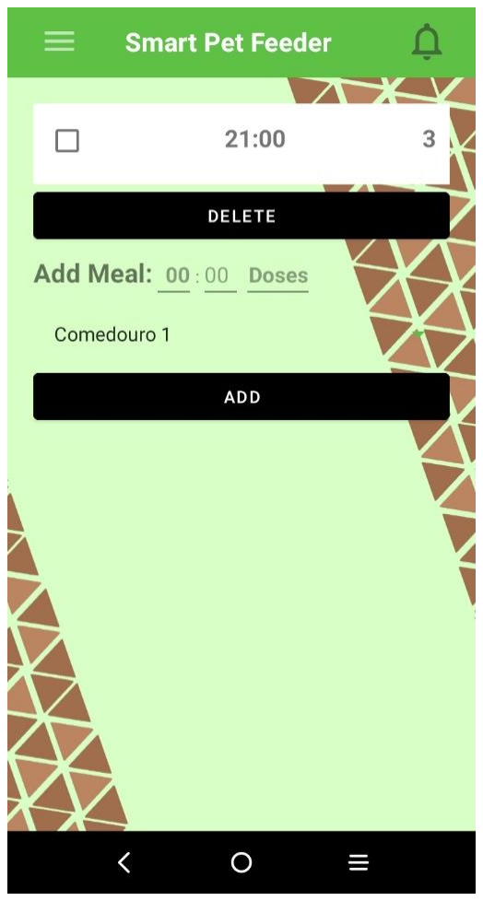
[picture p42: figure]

Figure 15 Schedule Screen

### 6.1 Delete a schedule meal

The user can delete a schedule meal by marking the exact meal and press the DELETE button, Fig.16.

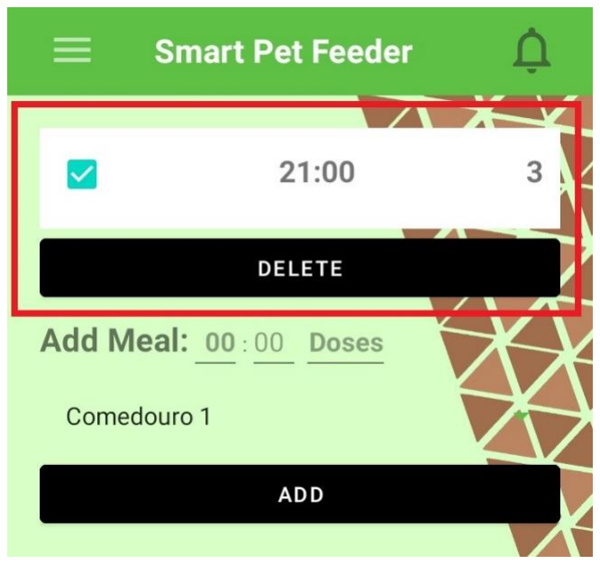
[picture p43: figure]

Figure 16 Schedule delete meal

P 10 | 20

### 6.3 Add a schedule meal

To add a schedule meal the user must fill the form with the number of the hour, minute, number of doses and select the feeder device to execute the meal and press the ADD button, Fig.17.

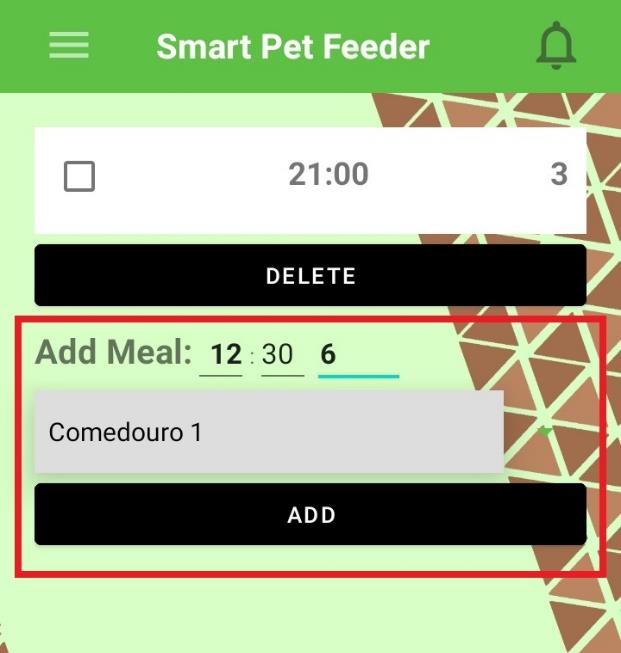
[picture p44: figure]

Figure 17 Add schedule meal form

Once the user presses the ADD button with the form filled the meal will automatically appear on the Schedule Screen and a message will appear on the bottom of the screen, Fig.18.

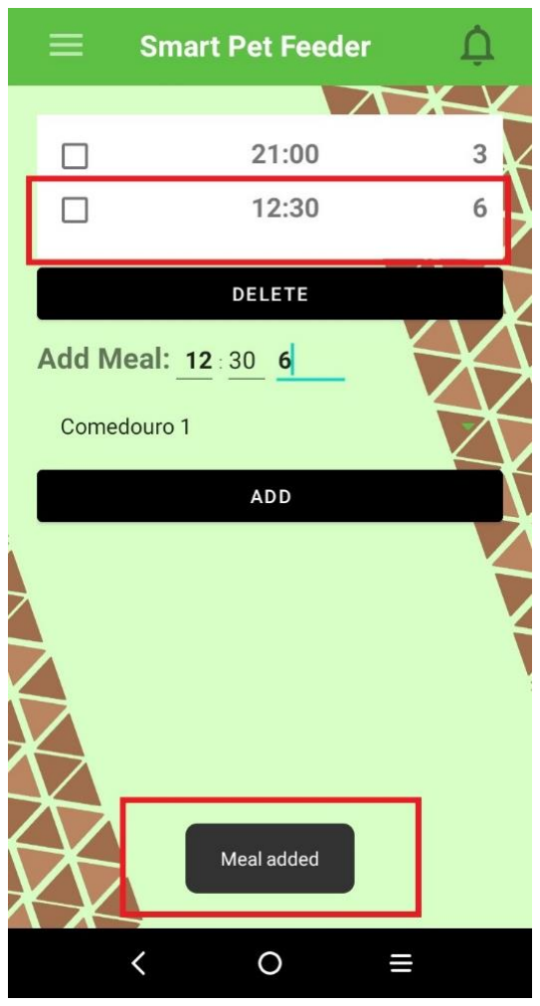
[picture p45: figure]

Figure 18 Added schedule meal

P 11 | 20

# 7. My Profile Screen

On the My Profile Screen, Fig.19, the user can check his profile data, which are their name, email and phone number.

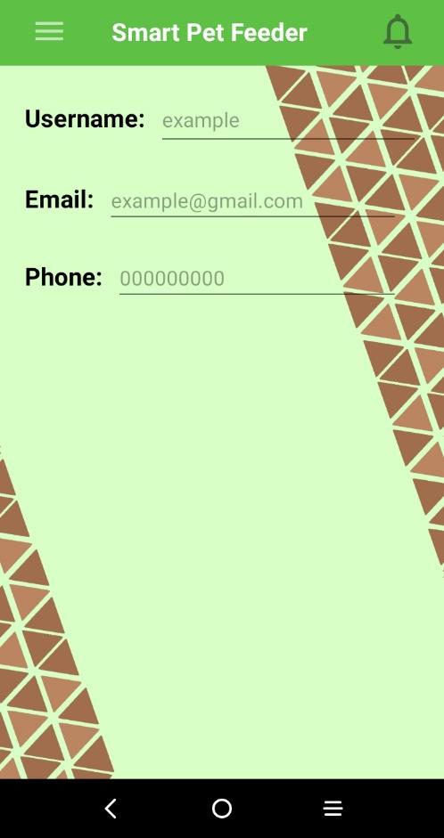
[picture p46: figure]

Figure 19 My Profile Screen

### 7.1 Update user information

The user can update their information by pressing in the space/spaces and write the new information over the old one.

Writing in any space will automatically turn the UPDATE button visible to the user, Fig.20. When pressed all the information written will change for the old one. If the operation is successfully executed a message on the bottom of the screen will appear, Fig.21.

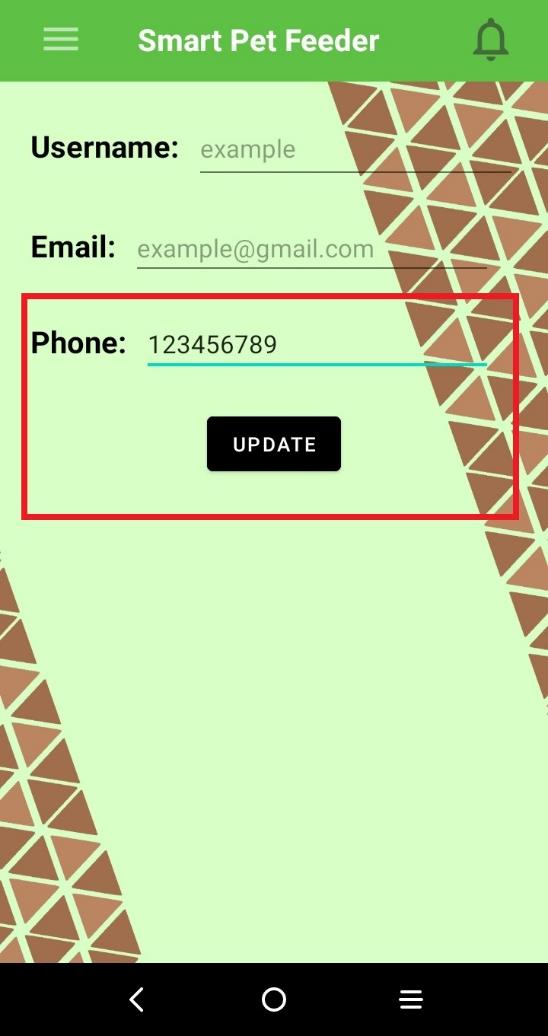
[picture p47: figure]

P 12 | 20

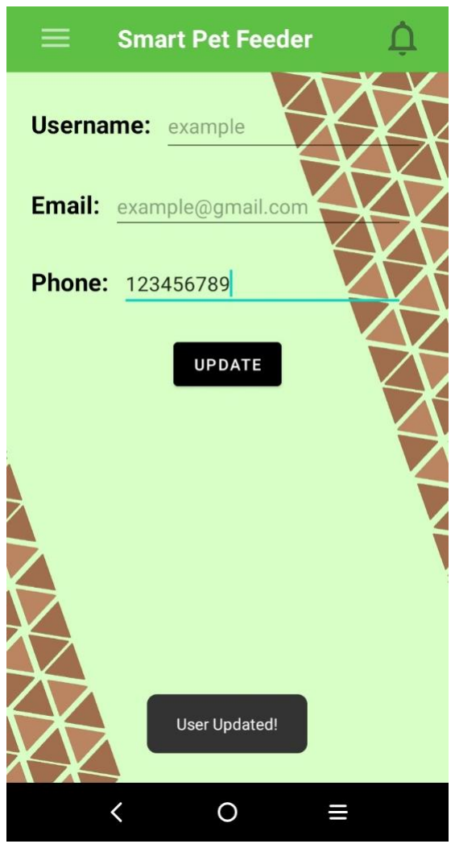
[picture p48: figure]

Figure 21 Update user form | Figure 20 My Vet association made

P 13 | 20

# 8. My Vet Screen

In the My Profile Screen, Fig.22, the user has access to the information of the pets that are associated with the feeder devices available to the user. To show the information the user must select the pet’s name on the select box.

Figure 22 My Vet Screen

### 8.1 Associate a pet to a device

The user can create and associate a pet to a feeder device, which is available to the user and isn’t associate to a pet already. To apply this method the user must fill the form above the CREATE button and then press it, Fig.23. If the procedure is successfully made then the user can already check the pet information by selecting the pet in the select box at the top of the screen, Fig.23.

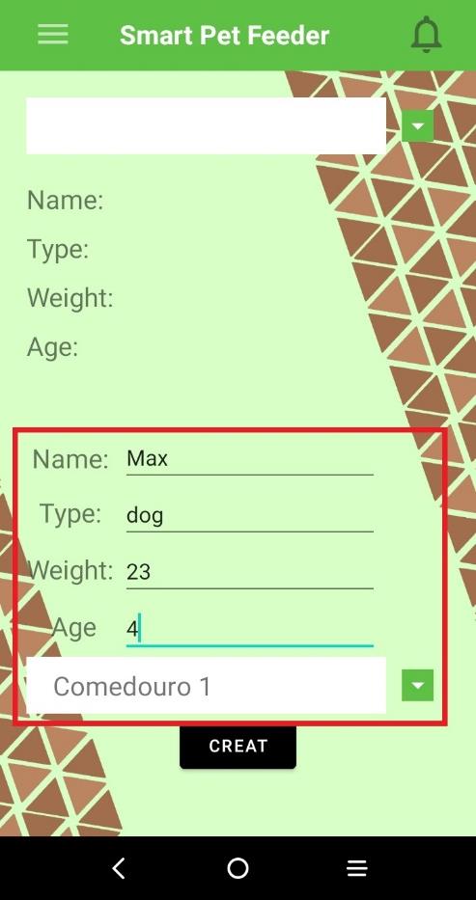
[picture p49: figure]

P 14 | 20

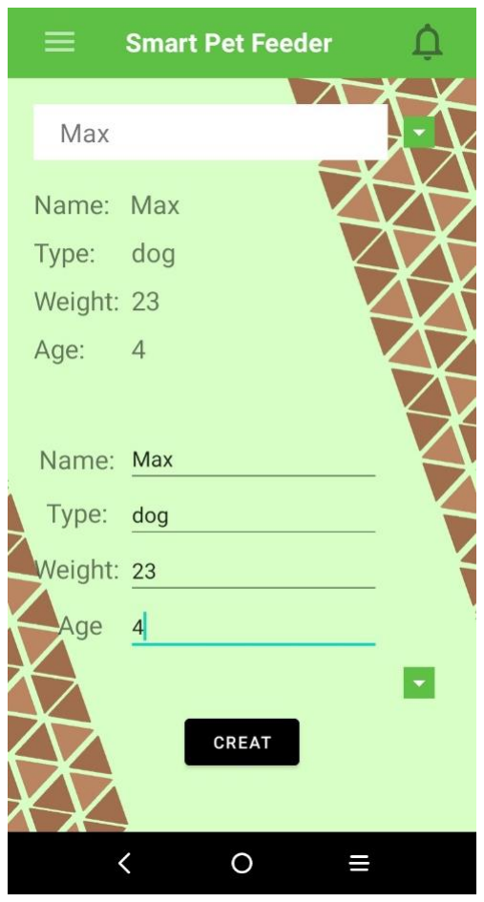
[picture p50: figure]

Figure 23 My Vet association form | Figure 24 My Vet association made

P 15 | 20

# 9.Notifications

The Notifications only can be access by the user when a notification is sent by the HUB. The user will be notified, int the app, by the notification icon on the top right of the screen, near of “Smart Pet Feeder”, Fig.25.

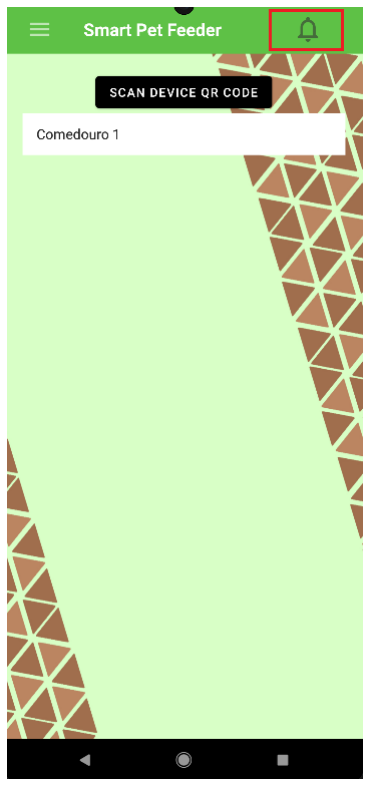
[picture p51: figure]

Figure 25 Notification icon

If the user has received a notification by the HUB the notification icon will change, Fig. 26 and Fig.27, and the notification icon will be show to the user in case the user pressesthe notification icon.

Figure 27 No notifications received | Figure 26 At least 1 notification received

P 16 | 20

When the user presses the notification icon a pop-up will appear with the description
of the notification, the level of priority and the feeder device. Then the user has 2 options, press CANCEL to close the pop-up and to maintain the notification or press CONFIRM to close the popup and delete the notification, Fig.28. Tapping outside of the pop-up will do the same action of pressing CANCEL.

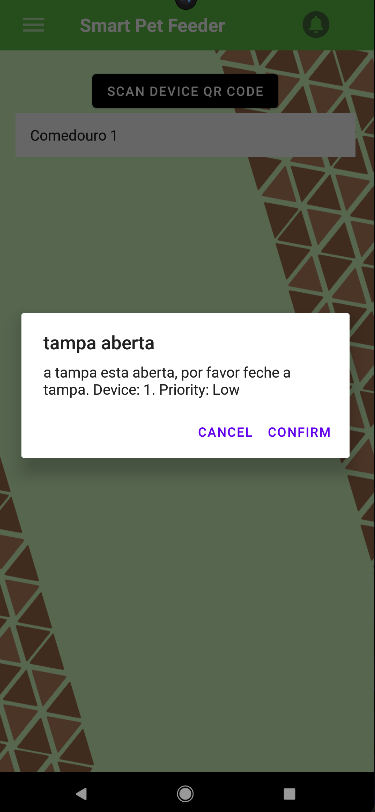
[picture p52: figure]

Figure 28 Notification open

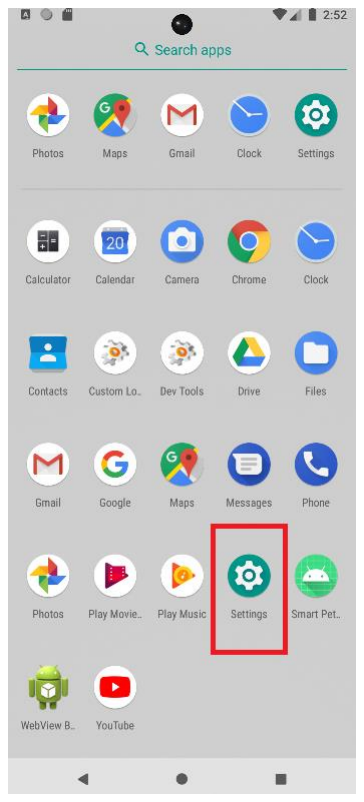
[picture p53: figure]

P 17 | 20

# 10. Errors

- In case the Login Screen form is correctly fill and the login doesn’t happen, first verify if the connection of the device is the same of the Central HUB. If the login still doesn’t work, then restart the app. If the login still doesn’t happen, then uninstall and install again the app or report the event to a technical.
- If the app doesn’t show any data in any screen, first verify if the connection of the device is the same of the Central HUB. If it is and still no data appear, logout the session and login again.
- If the Scan Device QR Code button is pressed and the phone’s camera doesn’t pop-up, go to Settings-> Apps & Notifications-> App permissions -> Camera and the make sure the toggle button at Smart Pet Feeder is on, Fig.29.

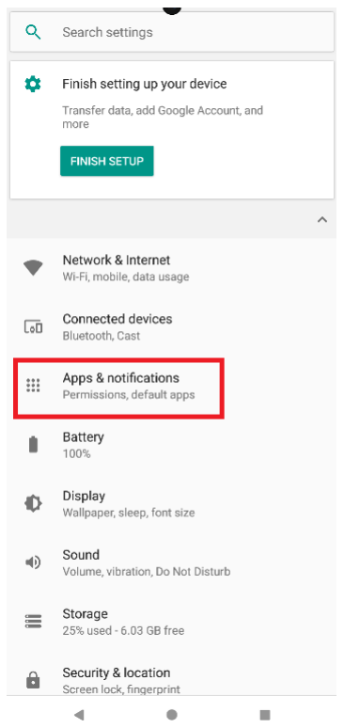
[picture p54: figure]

P 18 | 20

P 19 | 20

Figure 29 Smart Pet Feeder App, Camera Access

# 11. Attachments

### 11.1 App flow

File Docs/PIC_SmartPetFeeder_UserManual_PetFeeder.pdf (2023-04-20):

# SMART PET FEEDER

FEEDER DEVICE / CENTRAL HUB

USER MANUAL

P 1 | 13

# Index

P 2 | 13

# 1. Components description

### 1.1 Central HUB

### 1 Power cable, cable responsible for powering the Central HUB, should be

connected to an adapter with an output of 5V and inserted into a power plug near the device, Fig.1 and Fig.3.

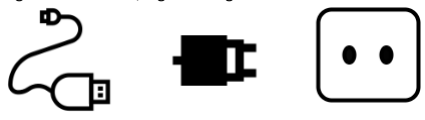
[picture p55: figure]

Figure 1 Central HUB, Power cable

2 Ethernet cable, the ethernet cable must be directly connected to the local Wi-Fi router, Fig.2 and Fig.3.

Figure 2 Central HUB, Ethernet cable

### 3 Central HUB, device responsible for managing the data between the

android APP and the Feeder Device, Fig.3.

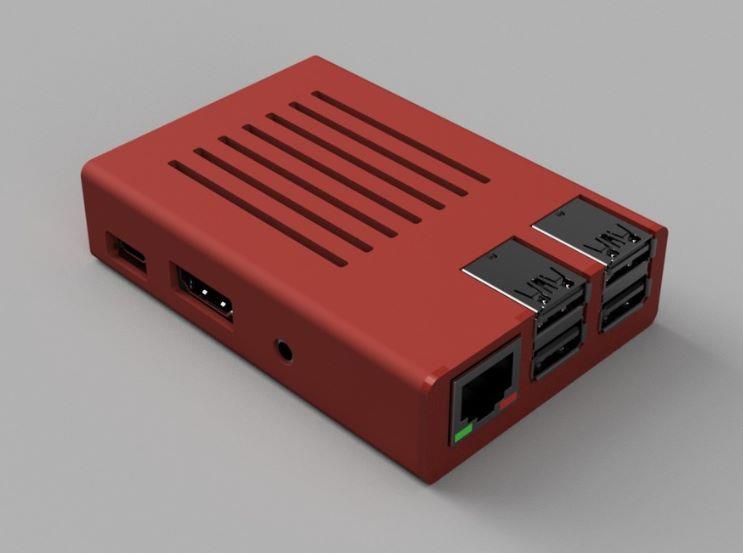
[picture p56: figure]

Figure 3 Central HUB, connections

P 3 | 13

### 1.2 Feeder Device

### 1. Power cable, cable responsible for powering the Feeder Device, should be

connected to an adapter with an output of 5V and inserted into a power plug near the device, Fig.1 and Fig.4.

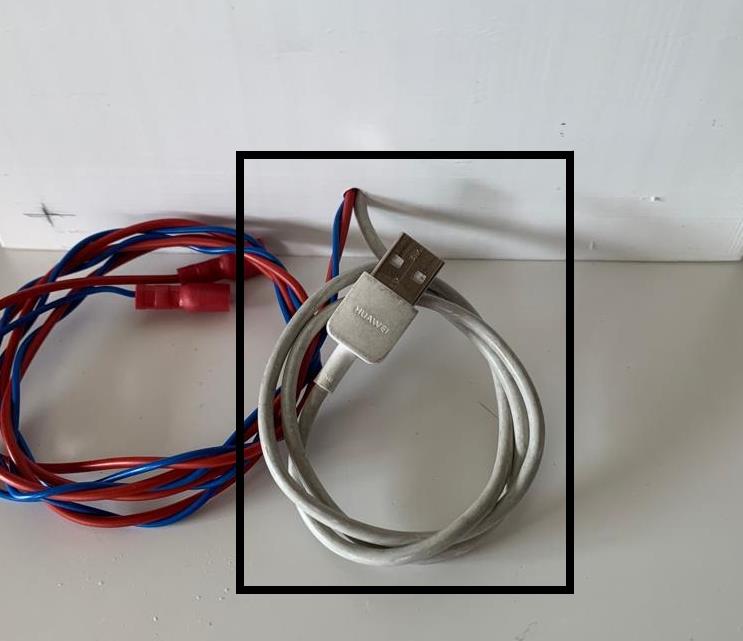
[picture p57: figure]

Figure 4 Feeder Device, Power cable

2. Water access point, small pipe to connect the water valve of the Feeder Device, Fig.5.

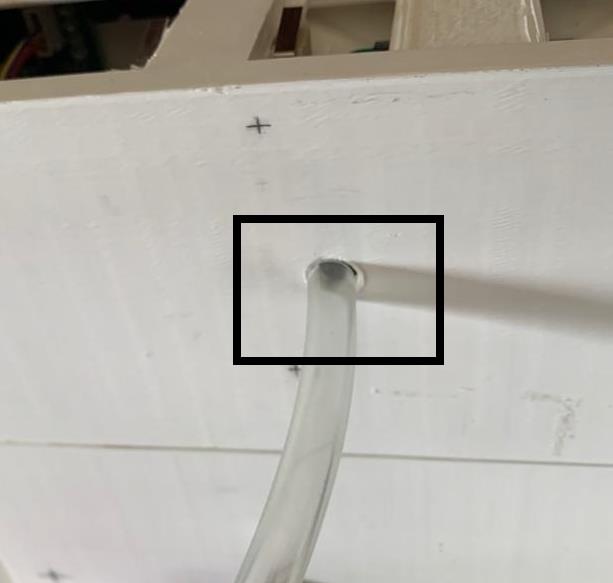
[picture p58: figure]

Figure 5 Feeder Device, Water access point

P 4 | 13

### 3. Water and Food bowls, part of the Feeder Device where the pet’s food and water

will be for the animal dispose, Fig.6.

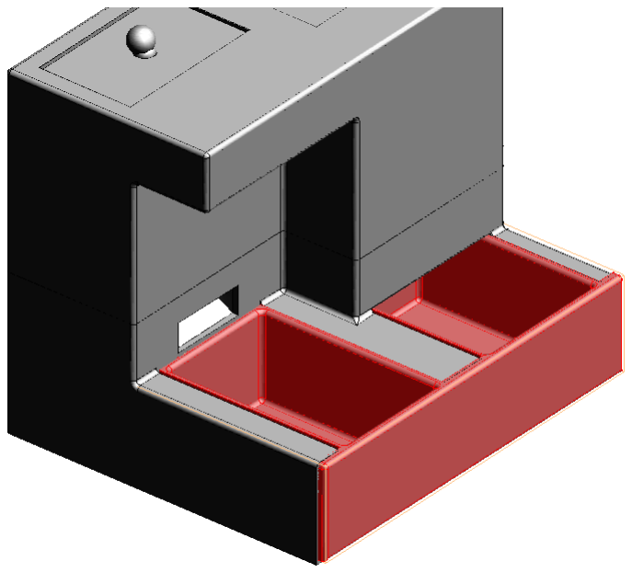
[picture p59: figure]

Figure 6 Feeder Device, water and food bowls

4. Deposit cover, covers the deposit of the pet’s food, Fig.7.

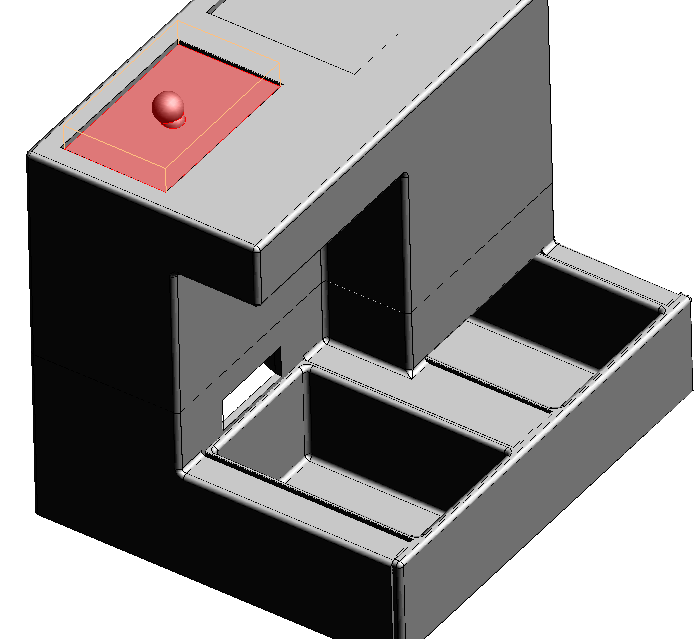
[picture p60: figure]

Figure 7 Feeder Device, deposit cover

P 5 | 13

# 2. Installation

To install the services of the Feeder Device and the Central HUB, as the first step, the user must connect the Ethernet cable (2) to the Central HUB and then connect the Power cable (1) to the Central HUB, Fig.8.

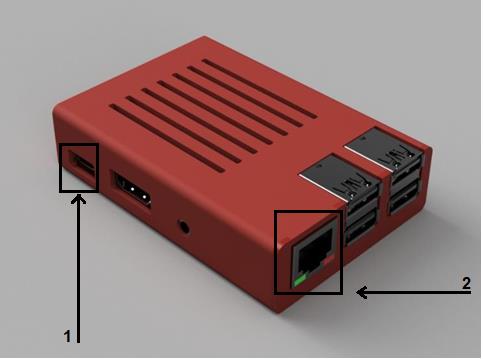
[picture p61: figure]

Figure 8 Installation of the Central HUB

After installing the Central HUB, the user must fill the deposit of the Feeder Device threw the Deposit cover, then connect a water supply to the Water access point and make sure it doesn’t leak. After that connect the Power cable to the Feeder Device.

The connection between the Central HUB and Feeder Device will be automatic, if the connection is correctly made then the green light will turn on, Fig.9.

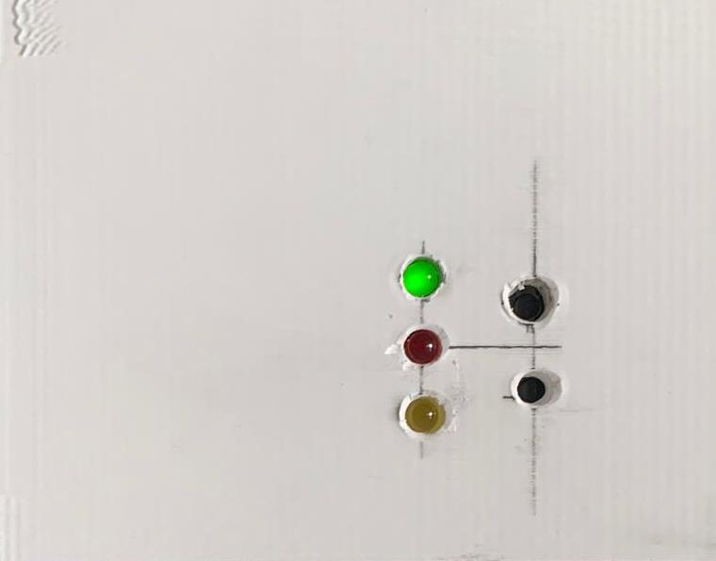
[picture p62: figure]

Figure 9 Feeder Device, connection Led

P 6 | 13

# 3. Cautions

### 3.1 Cautions with Central HUB

a) The Central HUB must be placed in an open space to guarantee the communication with the Feeder Device.
b) The Central HUB must be away from children and pets.
c) Must be away from heaters, or the case could melt.
d) Mustn’t be near of water or humid places.

### 3.2 Cautions with Feeder Device

a) Verify if the water pipe is correctly connected to the water access point.
b) The user must be cautious about water in contact with the Feeder Device, the contact with water must be only with the bowl and the water access point in case there is water in any other place, the device must be turned off immediately.
c) Verify if the deposit cover is fully closing the food entrance.
d) Make sure the food outlet is clear, Fig.10 and Fig.11.

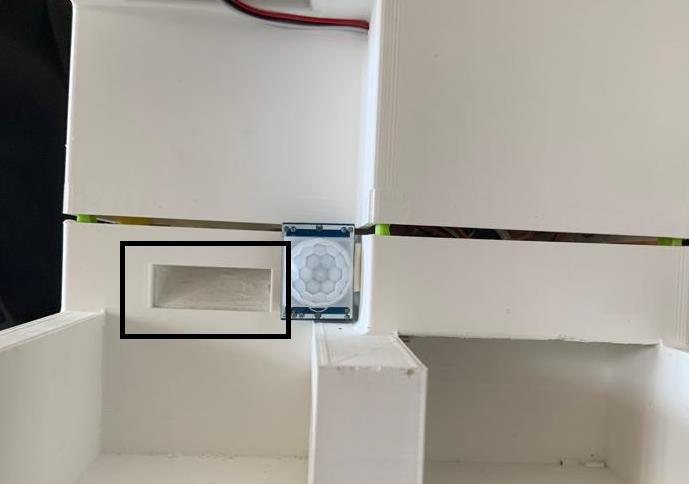
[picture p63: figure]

Figure 10 Food outlet

e) Perform maintenance on the sensors every 2 months, the dust from the food could change the sensors values, Fig.11 and Fig.12.

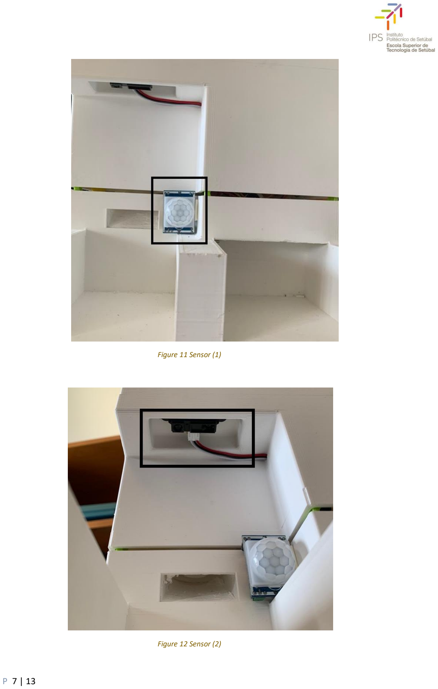
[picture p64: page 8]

P 7 | 13

Figure 11 Sensor (1)

Figure 12 Sensor (2)

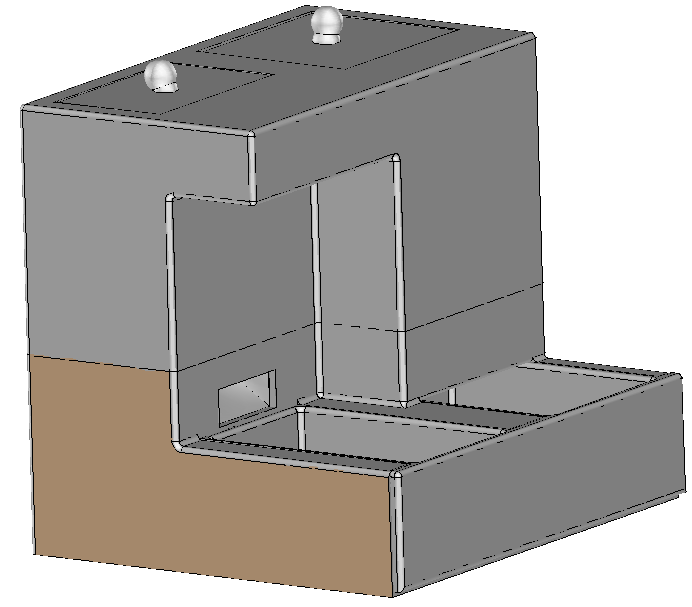
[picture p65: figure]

P 8 | 13
f) Make sure the food and water bowls are fully inserted into the Feeder Device or it will enter in safety mode, Fig.13.

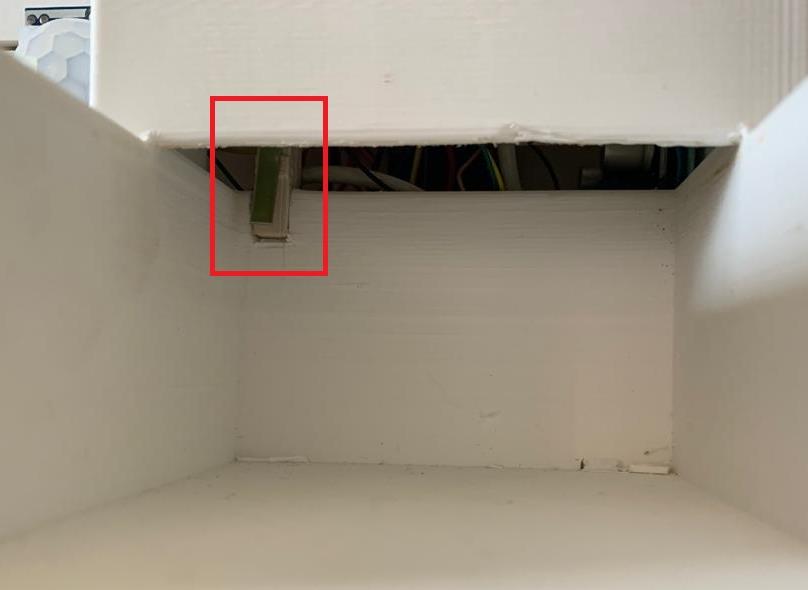
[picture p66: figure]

Figure 13 Bowls sensor

g) Always pick the Feeder Device from the bottom of the case, Fig.14 and Fig.15.

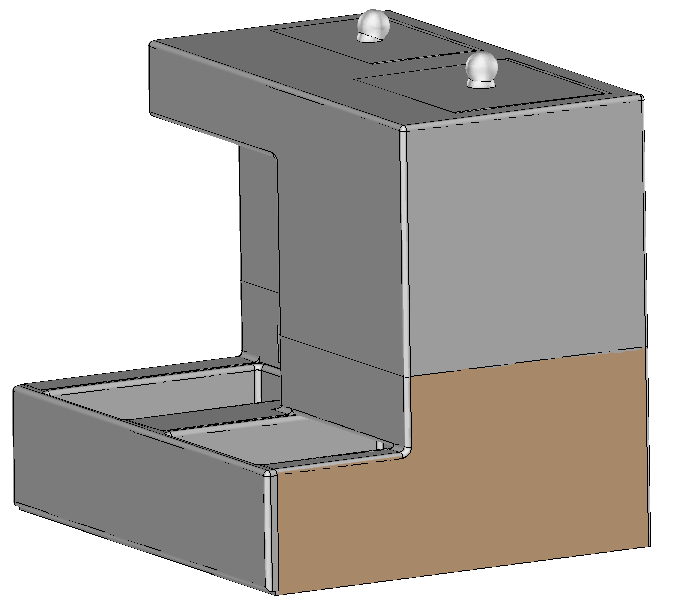
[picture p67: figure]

Figure 15 Feeder Device, hold safety zone left | Figure 14 Feeder Device, hold zone right

P 9 | 13

# 4. Errors

- In case the food doesn’t come out of the food outlet, first check if the red led is turn on, which means the deposit is almost empty, Fig.16. If food still doesn’t come out then verify the cautions c), d) and f).

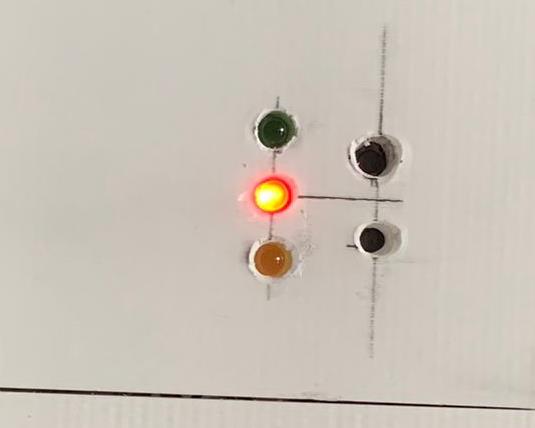
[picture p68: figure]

Figure 16 Feeder Device, red led

- If the Feeder Device drops food or water when unwanted and the Yellow led is turn on, Fig.17, verify cautions a), b) and e).

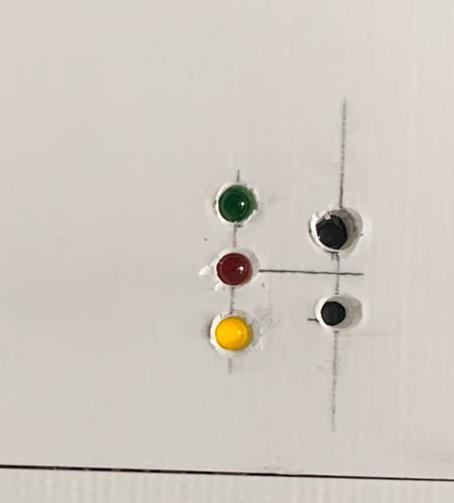
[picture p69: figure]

Figure 17 Feeder Device, yellow led

P 10 | 13
- If the Feeder Device doesn’t work and none of the led’s is turn on or blink, then press the RESET button, Fig.18. If the error remains, then pull out the power cable of the Feeder Device and the Central HUB and put it back on. If the error remains, then report the error to a technical.

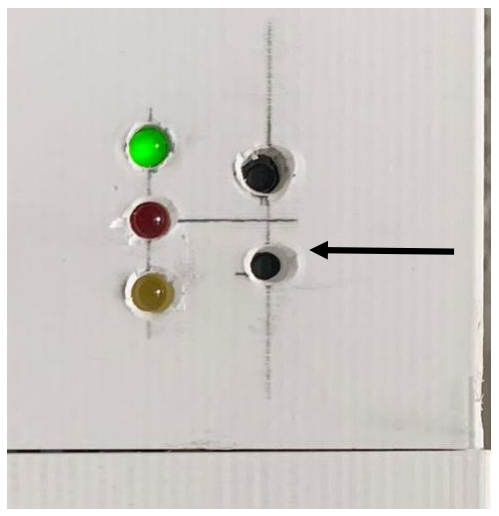
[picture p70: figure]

Figure 18 Feeder Device, reset button

# 5.Dashboard


P 11 | 13

The Dashboard can be accessed in any browser by searching “192.168.1.199:1880/ui”, if the same one is connected to same network as the Central HUB, Fig.19.

Figure 19 Dashboard

In the Dashboard the user can check if the deposit cover is open (1), the pet’s presence (2), the deposit level (3), water bowl level (4) and the food bowl level (5), Fig.20.

Figure 20 Dashboard description

P 12 | 13

# 6. Manual meal

To perform a manual meal, the user must press the Manual Meal button, Fig.21.


Figure 21 Feeder Device, manual meal button

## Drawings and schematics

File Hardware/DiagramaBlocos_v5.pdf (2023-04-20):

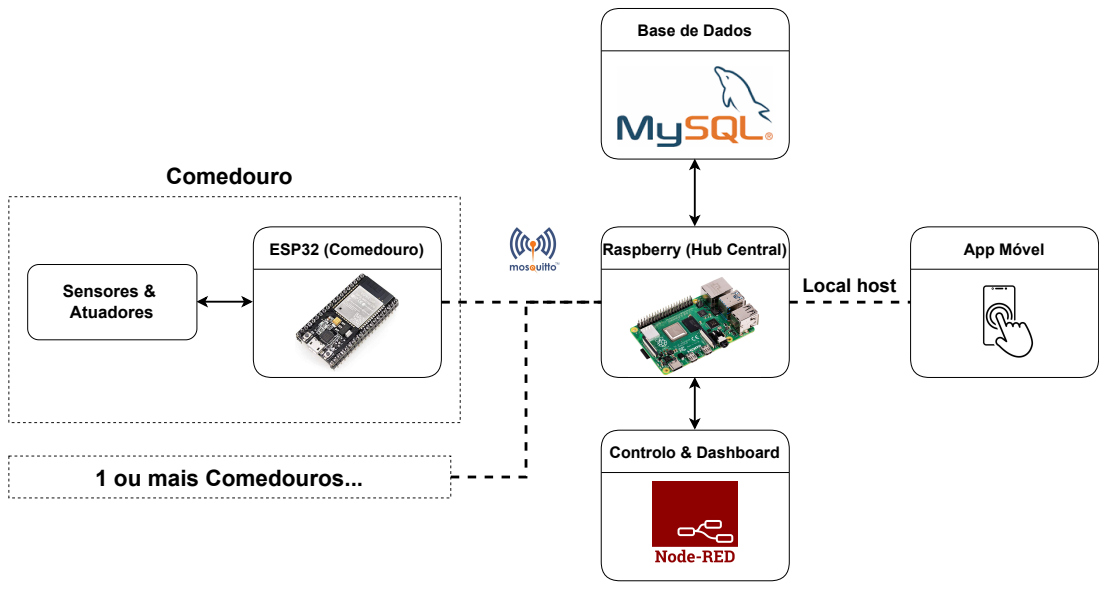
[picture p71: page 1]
Local host; Comedouro; Controlo & Dashboard; ESP32 (Comedouro); App Móvel; Sensores & Atuadores

Base de Dados

Raspberry (Hub Central)

1 ou mais Comedouros...

## Pet Feeder

## Central Hub

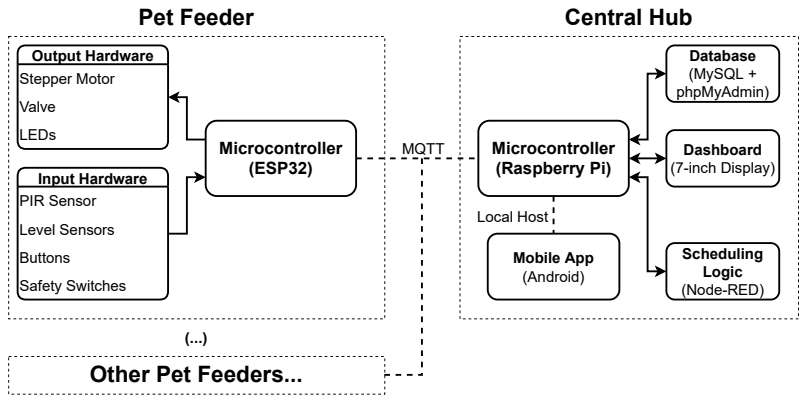
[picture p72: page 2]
MQTT; Microcontroller (ESP32); Output Hardware Stepper Motor; Valve; LEDs; Input Hardware PIR Sensor; Level Sensors; Buttons; Safety Switches; Local Host; Microcontroller (Raspberry Pi); Database (MySQL + phpMyAdmin); Scheduling Logic (Node-RED); Mobile App (Android); Dashboard (7-inch Display)

Other Pet Feeders...

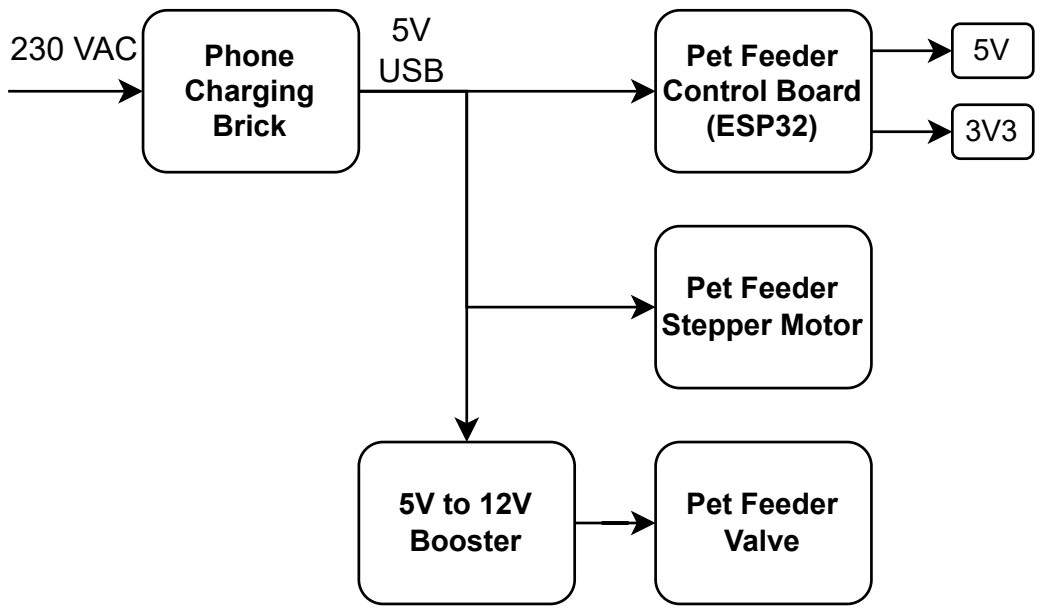
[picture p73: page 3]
Phone Charging Brick; Pet Feeder Control Board (ESP32); Pet Feeder Stepper Motor; Pet Feeder Valve; 5V to 12V Booster; USB 230 VAC

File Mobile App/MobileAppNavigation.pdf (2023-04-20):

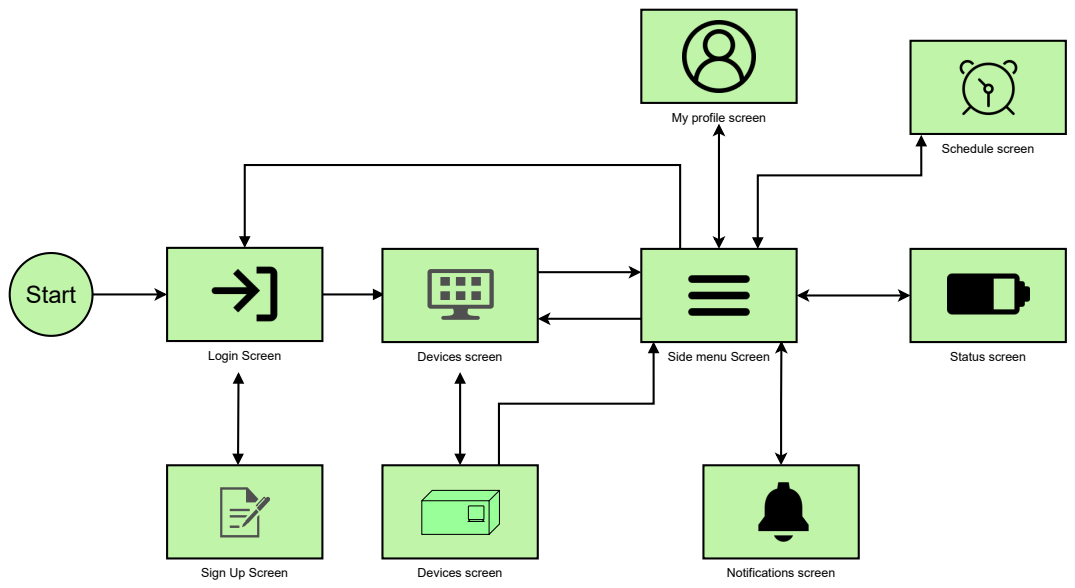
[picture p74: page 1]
Login Screen; Start; Devices screen; Schedule screen; Status screen; Notifications screen

My profile screen

Side menu Screen

Sign Up Screen

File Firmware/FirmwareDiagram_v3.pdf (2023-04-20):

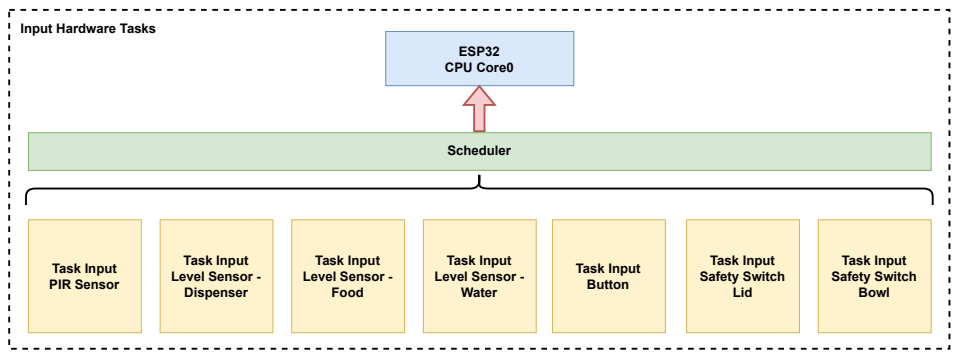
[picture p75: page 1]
Task Input Level Sensor - Dispenser; Task Input PIR Sensor; Task Input Button; Task Input Level Sensor - Food; Task Input Level Sensor - Water; Task Input Safety Switch Lid; Task Input Safety Switch Bowl; ESP32 CPU Core0; Scheduler

Input Hardware Tasks

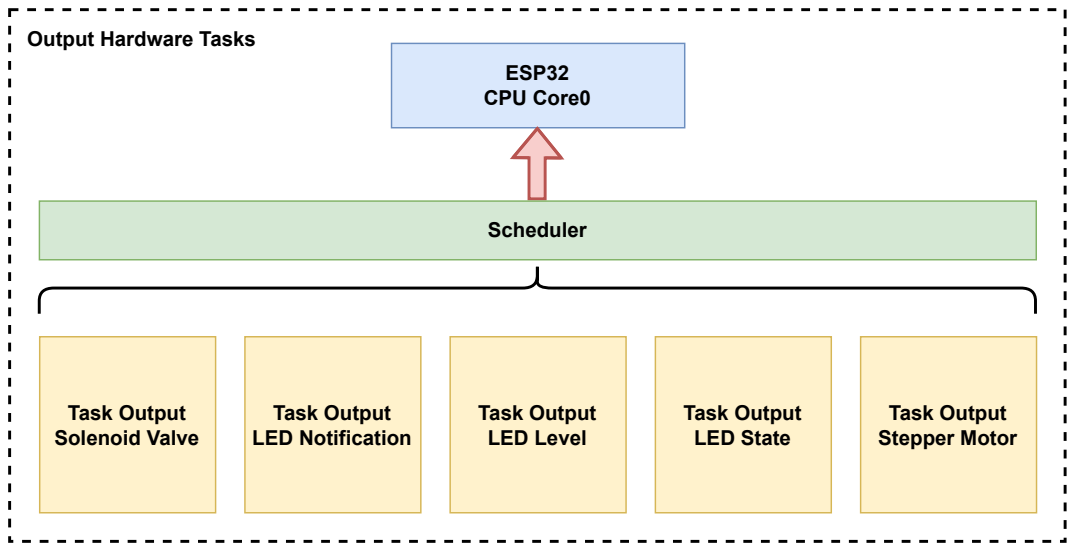
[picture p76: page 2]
ESP32 CPU Core0; Scheduler; Task Output Stepper Motor; Task Output Solenoid Valve; Task Output LED Notification; Task Output LED Level; Task Output LED State

Output Hardware Tasks

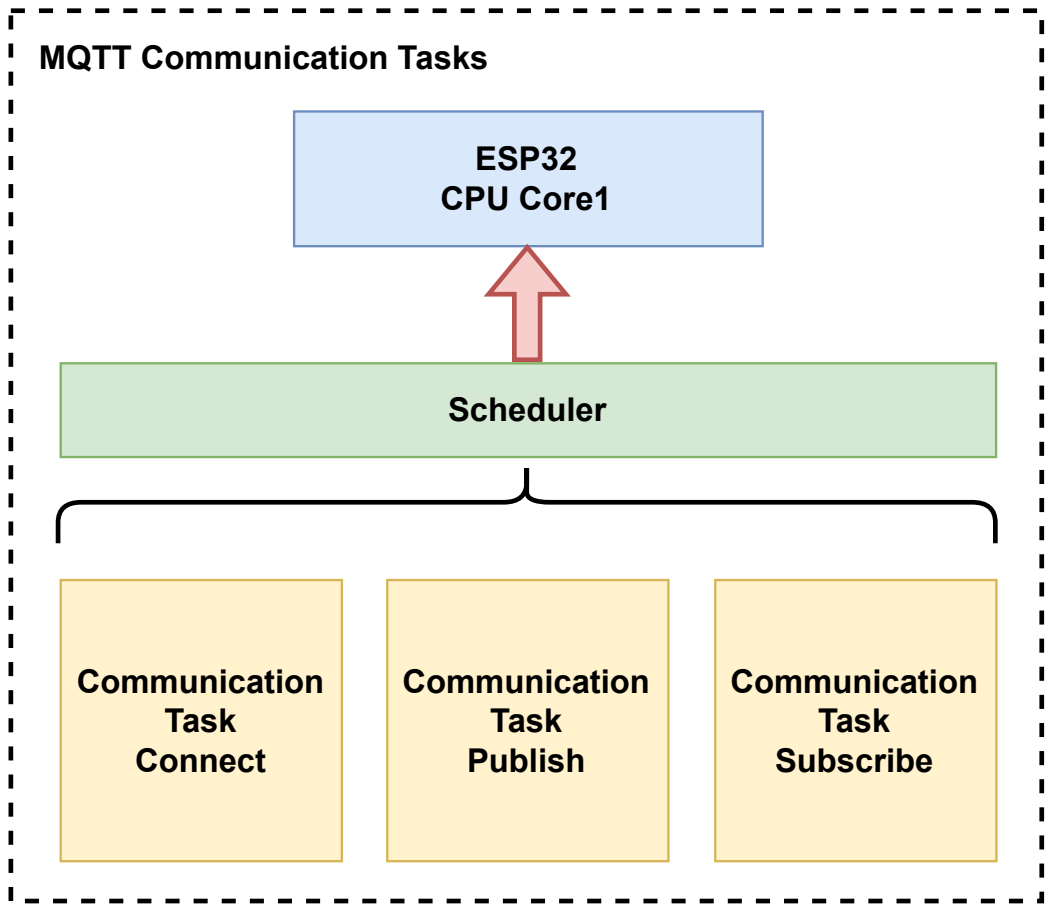
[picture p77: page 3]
ESP32 CPU Core1; Scheduler; Communication Task Connect; Communication Task Publish; Communication Task Subscribe

MQTT Communication Tasks

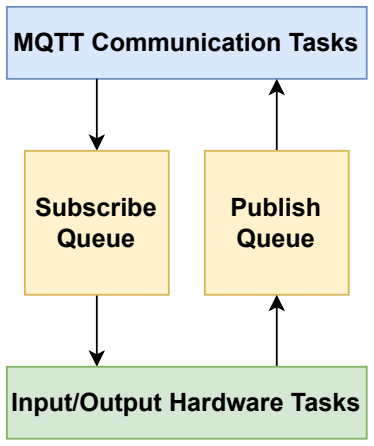
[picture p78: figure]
MQTT Communication Tasks; Subscribe Queue; Publish Queue; Input/Output Hardware Tasks
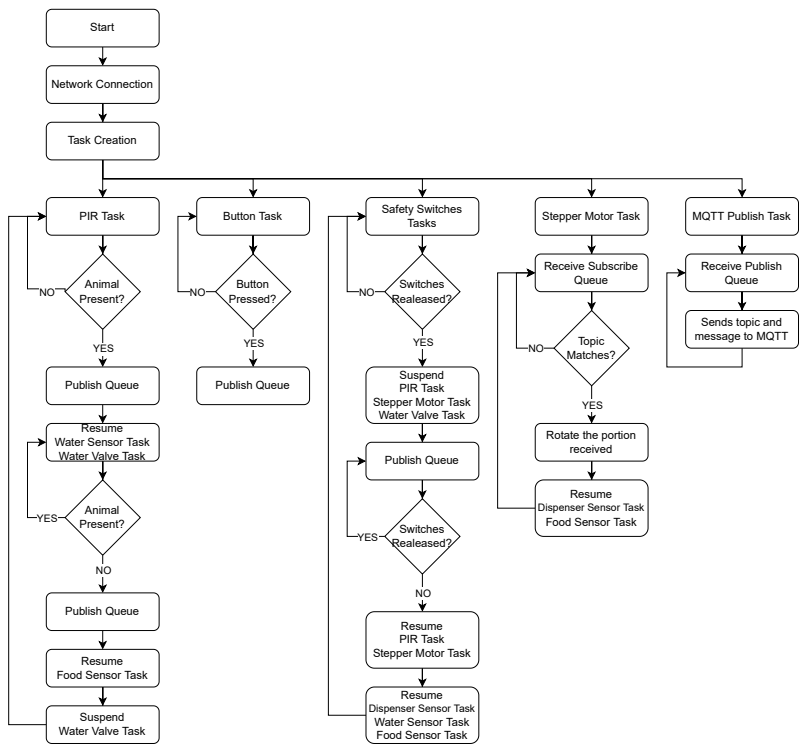
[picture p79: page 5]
Start; Network Connection; Task Creation; YES; Animal Present?; PIR Task; Button Task; Safety Switches; Tasks; Stepper Motor Task; MQTT Publish Task; Button Pressed?; Publish Queue; Switches Realeased?; Switches Realeased? YES; Receive Subscribe Queue; Topic Matches?; Receive Publish Queue

Sends topic and
message to MQTT

Suspend
PIR Task
Stepper Motor Task
Water Valve Task

Resume
Water Sensor Task

Rotate the portion
received

Dispenser Sensor Task
Food Sensor Task

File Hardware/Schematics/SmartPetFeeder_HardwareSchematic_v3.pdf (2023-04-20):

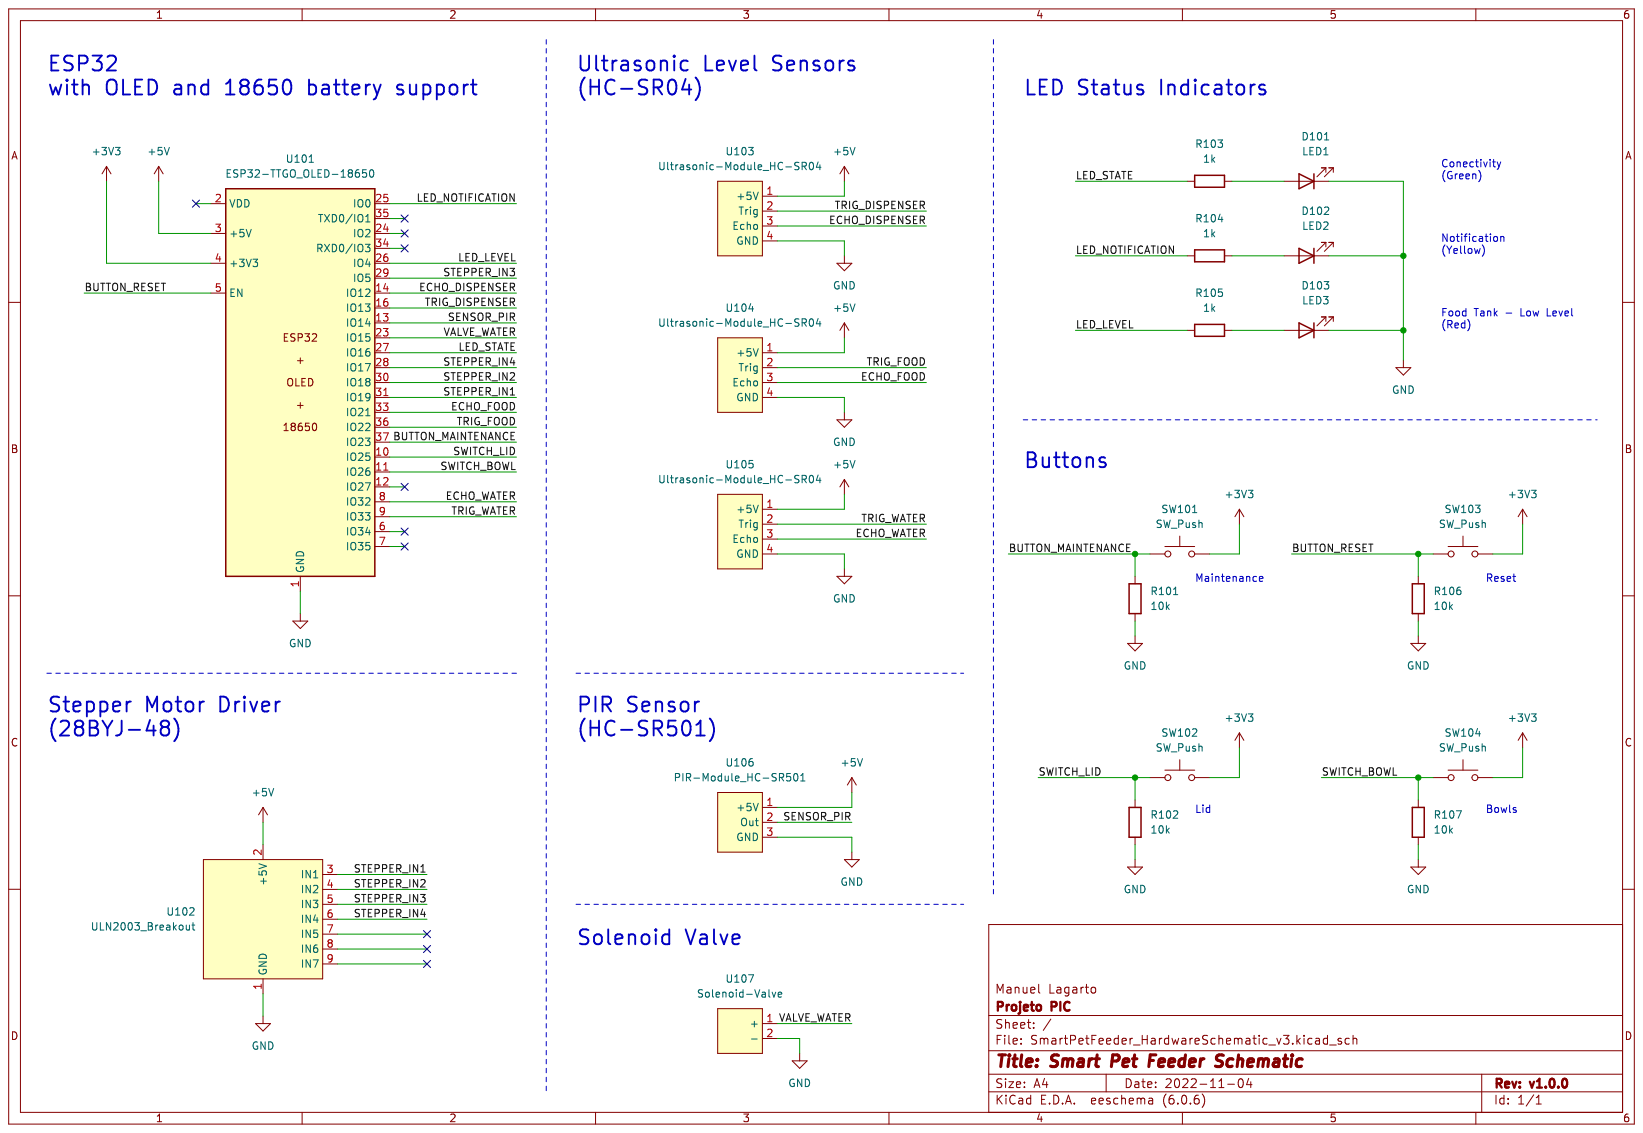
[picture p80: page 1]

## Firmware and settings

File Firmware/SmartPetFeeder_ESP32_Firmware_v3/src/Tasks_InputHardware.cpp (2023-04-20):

#include "Tasks_InputHardware.h"

int32_t compute_distance_percentage(bool sensorType, uint32_t inputDistance) {
  // sensorType = 0 : Sharp IR (Bowls)
  // sensorType = 1 : Ultrasonic Sensor (Dispenser)
  const uint32_t maxDistance_type0 = 9;  // Empty (9)
  const uint32_t minDistance_type0 = 6;   // Full (6)

  const uint32_t maxDistance_type1 = 5;  // Empty (9)
  const uint32_t minDistance_type1 = 2;   // Full (6)

  int32_t range;
  int32_t measuredRange;

  if(sensorType == 0) {
    range = maxDistance_type0 - minDistance_type0;
    measuredRange = inputDistance - minDistance_type0;
  }
  else if (sensorType == 1) {
    range = maxDistance_type1 - minDistance_type1;
    measuredRange = inputDistance - minDistance_type1;
  }
  
  int32_t inputPercentage = 100-((measuredRange*100)/range);

  if(inputPercentage > 100) {
    inputPercentage = 100;
  }
  else if(inputPercentage < 0) {
    inputPercentage = 0;
  }

  return inputPercentage;
}

// Reads PIR sensor input
// !!!Task control for level sensors needs to be implemented!!!
void pirSensor_task(void * parameter) {
  static uint8_t pirState = LOW;
  static uint8_t lastState = LOW;
  
  // Create a message struct to send to publish_task
  message_t message;

  // Copy the characters from the topic macro to the mqttTopic field
  for (int i = 0; i < sizeof(message.mqttTopic); i++) {
    message.mqttTopic[i] = MQTT_PUB_SENSOR_PIR[i];
    if (MQTT_PUB_SENSOR_PIR[i] == '\0') {
      break;
    }
  }

  // Task infinite loop
  while(true) {
    pirState = digitalRead(SENSOR_PIR_GPIO_INPUT);

    if(pirState != lastState) {
      // Checks if current state is HIGH AND != from lastState
      if(pirState == LOW) {
        Serial.println("\nMovement not Dectected");

        // If state goes LOW, waits a few seconds to check if state goes HIGH
        // Blocking time 2.5s (HC-SR501 datasheet)
        vTaskDelay(2500 / portTICK_PERIOD_MS);

        pirState = digitalRead(SENSOR_PIR_GPIO_INPUT);
        if(pirState == LOW) {
          // Falling edge trigger after chencking if PIR is definitely LOW
          Serial.println("pirSensor_task state sent");

          // Converts button_state to char arr
          sprintf(message.mqttMessage, "%d", pirState);

          // Send the message struct to the publish_task via publish_queue
          xQueueSend(publish_queue, &message, 0);

          // Resumes food bowl level sensor reading task
          vTaskResume(TaskHandle_FoodSensor);
          // Resumes water bowl level sensor reading task
          vTaskResume(TaskHandle_WaterSensor);
        }
      }
      else {        
        Serial.println("\nMovement Detected");
        Serial.println("pirSensor_task state sent");

        // Converts button_state to char arr
        sprintf(message.mqttMessage, "%d", pirState);

        // Send the message struct to the publish_task via publish_queue
        xQueueSend(publish_queue, &message, 0);

        // Resumes water bowl level sensor reading task
        //vTaskResume(TaskHandle_WaterSensor);
      }
      lastState = pirState;
    }
    else if(pirState == HIGH) {
      // Resumes water bowl level sensor reading task
      vTaskResume(TaskHandle_WaterSensor);
    }

    vTaskDelay(500 / portTICK_PERIOD_MS);   // Task delay in ms
  }
}

void levelSensor_dispenser_task(void* pvParameters) {
  uint64_t waveDuration;  // Wave sound duration
  uint64_t sensorDistance;      // Measured distance
  static uint64_t distanceMean;  // Measured distance after mean
  uint8_t samples = 5;

  // Create a message struct to send to publish_task
  message_t message;

  // Copy the characters from the topic macro to the mqttTopic field
  for (int i = 0; i < sizeof(message.mqttTopic); i++) {
    message.mqttTopic[i] = MQTT_PUB_SENSOR_DISPENSER[i];
    if (MQTT_PUB_SENSOR_DISPENSER[i] == '\0') {
      break;
    }
  }

  // Clear trigger pin
  digitalWrite(TRIG_DISPENSER_GPIO_OUTPUT, LOW);
  vTaskDelay(0.002 / portTICK_PERIOD_MS);   // Task delay in us

  while(true) {
    // Suspends food dispenser level sensor reading task
    vTaskSuspend(TaskHandle_DispenserSensor);
    Serial.println("\nlevelSensor_dispenser_task initialized");
    
    // Sets trigger pin HIGH for 10us 
    digitalWrite(TRIG_DISPENSER_GPIO_OUTPUT, HIGH);
    vTaskDelay(0.010 / portTICK_PERIOD_MS);   // Task delay in us
    digitalWrite(TRIG_DISPENSER_GPIO_OUTPUT, LOW);
    
    // Reads the echo pin
    waveDuration = pulseIn(ECHO_DISPENSER_GPIO_INPUT, HIGH);

    // Calculates the distance
    sensorDistance = (waveDuration * 0.034) / 2;
    Serial.println(sensorDistance);

    // Compute percentage: 0 = Sharp IR Level Sensor
    uint32_t sensorPercentage = compute_distance_percentage(1, sensorDistance);

    // Converts value to char arr
    sprintf(message.mqttMessage, "%d", sensorDistance);
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

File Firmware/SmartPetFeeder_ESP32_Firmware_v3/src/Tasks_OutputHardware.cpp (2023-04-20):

#include "Tasks_OutputHardware.h"

void solenoid_valve_task(void* pvParameters) {
  // MQTT data struct
  message_t message;

  while(true) {
    if(subscribe_queue != 0) {
      // Peeks topic and message from subscribe queue
      if(xQueuePeek(subscribe_queue, &(message), (TickType_t)10)) {
        // Check the received MQTT topic and message
        if(strcmp(message.mqttTopic, MQTT_SUB_VALVE_WATER) == 0) {
          // Received topic equals expected topic
          // Clears buffer from queue
          xQueueReceive(subscribe_queue, &message, portMAX_DELAY);
          
          Serial.println("Message received on LED");
          Serial.println(message.mqttTopic);
          Serial.println(message.mqttMessage);

          int value = atoi(message.mqttMessage);
          if(value == 0) {
            digitalWrite(VALVE_WATER_GPIO_OUTPUT, LOW);
          }
          if(value == 1) {
            digitalWrite(VALVE_WATER_GPIO_OUTPUT, HIGH);
          }
        }
      }
    }
    vTaskDelay(100 / portTICK_PERIOD_MS);
	}  
}

void led_notification_task(void* pvParameters) {
	// MQTT data struct
  message_t message;

	while(true) {
    if(subscribe_queue != 0) {
      // Peeks topic and message from subscribe queue
      if(xQueuePeek(subscribe_queue, &(message), (TickType_t)10)) {
        // Check the received MQTT topic and message
        if(strcmp(message.mqttTopic, MQTT_SUB_LED_NOTIFICATION) == 0) {
          // Received topic equals expected topic
          // Clears buffer from queue
          xQueueReceive(subscribe_queue, &message, portMAX_DELAY);
          
          Serial.println("Message received on LED");
          Serial.println(message.mqttTopic);
          Serial.println(message.mqttMessage);

          int value = atoi(message.mqttMessage);
          if(value == 0) {
            digitalWrite(LED_NOTIFICATION_GPIO_OUTPUT, LOW);
          }
          if(value == 1) {
            digitalWrite(LED_NOTIFICATION_GPIO_OUTPUT, HIGH);
          }
        }
      }
    }
    vTaskDelay(100 / portTICK_PERIOD_MS);
	}  
}

void led_level_task(void* pvParameters) {
  // MQTT data struct
  message_t message;

	while(true) {
    if(subscribe_queue != 0) {
      // Peeks topic and message from subscribe queue
      if(xQueuePeek(subscribe_queue, &(message), (TickType_t)10)) {
        // Check the received MQTT topic and message
        if(strcmp(message.mqttTopic, MQTT_SUB_LED_LEVEL) == 0) {
          // Received topic equals expected topic
          // Clears buffer from queue
          xQueueReceive(subscribe_queue, &message, portMAX_DELAY);
          
          Serial.println("Message received on LED");
          Serial.println(message.mqttTopic);
          Serial.println(message.mqttMessage);

          int value = atoi(message.mqttMessage);
          if(value == 0) {
            digitalWrite(LED_LEVEL_GPIO_OUTPUT, LOW);
          }
          if(value == 1) {
            digitalWrite(LED_LEVEL_GPIO_OUTPUT, HIGH);
          }
        }
      }
    }
    vTaskDelay(100 / portTICK_PERIOD_MS);
	}
}

void led_state_task(void* pvParameters) {
  // MQTT data struct
  message_t message;

	while(true) {
    if(subscribe_queue != 0) {
      // Peeks topic and message from subscribe queue
      if(xQueuePeek(subscribe_queue, &(message), (TickType_t)10)) {
        // Check the received MQTT topic and message
        if(strcmp(message.mqttTopic, MQTT_SUB_LED_STATE) == 0) {
          // Received topic equals expected topic
          // Clears buffer from queue
          xQueueReceive(subscribe_queue, &message, portMAX_DELAY);
          
          Serial.println("Message received on LED");
          Serial.println(message.mqttTopic);
          Serial.println(message.mqttMessage);

          int value = atoi(message.mqttMessage);
          if(value == 0) {
            digitalWrite(LED_STATE_GPIO_OUTPUT, LOW);
          }
          if(value == 1) {
            digitalWrite(LED_STATE_GPIO_OUTPUT, HIGH);
          }
        }
      }
    }
    vTaskDelay(100 / portTICK_PERIOD_MS);
	}
}

void stepper_motor_task(void* pvParameters) {
  const uint8_t feeder_div = 5;                                 // Number of feeder divisions
  const uint16_t steps_perRevolution = 2048;                    // Steps for each 360 rotation
  const uint16_t steps_perDiv = steps_perRevolution/feeder_div; // Steps for each feeder division
  //int8_t stepper_dir = 1;

  // Stepper definition
  Stepper stepper_feeder(steps_perRevolution, 
                         STEPPER_IN1_GPIO_OUTPUT,
                         STEPPER_IN2_GPIO_OUTPUT,
                         STEPPER_IN3_GPIO_OUTPUT,
                         STEPPER_IN4_GPIO_OUTPUT);
  // Set stepper speed [rpm]
  stepper_feeder.setSpeed(3);

	// MQTT data struct
  message_t message;

  while(true) {
    if(subscribe_queue != 0) {
      // Peeks topic and message from subscribe queue
      if(xQueuePeek(subscribe_queue, &(message), (TickType_t)10)) {
        // Check the received MQTT topic and message
        if(strcmp(message.mqttTopic, MQTT_SUB_MOTOR_FOOD) == 0) {
          // Received topic equals expected topic
          // Clears buffer from queue
          xQueueReceive(subscribe_queue, &message, portMAX_DELAY);
          
          Serial.println("Message received on MOTOR");
          Serial.println(message.mqttTopic);
          Serial.println(message.mqttMessage);

          int portions = atoi(message.mqttMessage);
          Serial.println(portions);
          if(portions != 0) {
            Serial.print("Stepper Moving...");
            for(int i=0; i<portions; i++) {
              stepper_feeder.step(steps_perDiv);
              vTaskDelay(500 / portTICK_PERIOD_MS);   // Task delay in ms
            }
            Serial.println("Stepper Stopped");

            // Resumes food bowl level sensor reading task
            vTaskResume(TaskHandle_FoodSensor);
            // Resumes food dispenser level sensor reading task
            vTaskResume(TaskHandle_DispenserSensor);
          }
        }
      }
    }
    vTaskDelay(100 / portTICK_PERIOD_MS);
  }
}

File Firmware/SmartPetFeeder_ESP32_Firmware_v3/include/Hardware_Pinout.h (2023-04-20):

/*
* == ESP32: Smart Pet Feeder Hardware Pinout ==
* 
* - Part of Smart Pet Feeder ESP32 Firmware:
* > pin numbers for the ESP32 based on the defined hardware design
*/

#ifndef HARDWARE_PINOUT_H
#define HARDWARE_PINOUT_H

// PIR Sensor
#define SENSOR_PIR_GPIO_INPUT 13

// Ultrassonic Level Sensors
#define TRIG_DISPENSER_GPIO_OUTPUT 14
#define ECHO_DISPENSER_GPIO_INPUT 27

//#define TRIG_FOOD_GPIO_OUTPUT 27
//#define ECHO_FOOD_GPIO_INPUT 26
#define SENSOR_FOOD_GPIO_INPUT 39   // ADC1_CH3

//#define TRIG_WATER_GPIO_OUTPUT 25
//#define ECHO_WATER_GPIO_INPUT 33
#define SENSOR_WATER_GPIO_INPUT 33  // ADC1_CH5

// Switches / Buttons
#define SWITCH_LID_GPIO_INPUT 32
#define SWITCH_BOWL_GPIO_INPUT 35
#define BUTTON_MAINTENANCE_GPIO_INPUT 34

// Solenoid Valve
#define VALVE_WATER_GPIO_OUTPUT 15

// Status LEDs
#define LED_NOTIFICATION_GPIO_OUTPUT 0
#define LED_LEVEL_GPIO_OUTPUT 4
#define LED_STATE_GPIO_OUTPUT 16

// Stepper Motor
#define STEPPER_IN4_GPIO_OUTPUT 17
#define STEPPER_IN3_GPIO_OUTPUT 5
#define STEPPER_IN2_GPIO_OUTPUT 18
#define STEPPER_IN1_GPIO_OUTPUT 19

// Reserved Pins
#define RESERVED2_GPIO 2
#define RESERVED21_GPIO 21
#define RESERVED22_GPIO 22
#define RESERVED23_GPIO 23


#endif
